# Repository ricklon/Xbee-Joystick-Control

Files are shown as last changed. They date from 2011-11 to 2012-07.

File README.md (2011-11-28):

#Xbee Joystick Controlled Robot

This project configures a set of Xbees that are plugged into a custom Joystick PCB, and wired on top of a line following Arduino based robot.
The robot project is here: http://ieee.rutgers.edu/content/line-following-kit

The current custom circuit boards for the project are kept in the Fritzing folder. In there there is a Fritzing for the Joystick, list of materials, and example etchable PCB files.

In order to wire the Xbee to the Arduino board you'll need to either use the custom circuit board in the Fritzing file, or you can bread board it on thop of the motor shield.

##Xbee programming for receiver, and sending

Note: This project currently uses Xbee series 1. They work fine and are well documented. 
I recommend using the Xbee Explorer (USB) or the Adafruit Xbee Adapter Kit (FTDI).

You will need a terminal program to configure the Xbees. One program that works on Windows, Mac, and Linux is Cool Term. You can find it here: http://freeware.the-meiers.org/

The configuration for the reciever Xbee should be:
+++//Wait for the OK, do not hit enter

```
+++ 
ATDL407B2C9A,DH0013A200,ID 2001,MY20, WR, CN
```

The configuraiton for the Joystick sender Xbee should be:
+++//Wait for the OK, do not hit enter

```
+++
ATDL407E10E6, DH0013A200, ID2001, MY10, D02, D12, D22, IR64, WR, CN
```

You can check the Xbee configuration with the following:
+++//Wait for the OK, do not hit enter

```
+++
ATDL, DH, ID, MY, D0, D1, D2, IR, CN
```

##Xbee robot receiver configuration
The bread boarding step requires the following parts:
Xbee breadboard adapter
4 wires
tiny breadboard

The Xbee adapter is wired in with the following pins:
Xbee --> Arduino
pin 1  -> 3.3v
pin 10 -> ground
pin 2 -> 0
pin 3 -> 1

It's easiest to do the wiring first. Then place the Xbee adapter on the tiny breadboard.

##Arduino Sketch
Make sure the Xbee Rx,Tx pins are disconneted from the Arduino. The Arduino Uno use the default serial port for Xbee and programming Arduino.

The upload the following sketch for the Joystick controls:
https://github.com/ricklon/Xbee-Joystick-Control/blob/master/arduino/XbeeControlledRobot256uno/XbeeControlledRobot256uno.pde

##Python code
This is only needed to diagnose communication issues. Not needed, but interesting.

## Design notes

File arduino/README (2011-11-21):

Each of these files are examples of elements need to debug the Xbee controlled robot.

The completed robot that will work on all Arduino's using the IEEE Rutgers  motorshield can use:
XbeeControledRobot256uno

The controls work OK.

The configuration for the reciever Xbee should be:
+++
ATDL407B2C9A,DH0013A200,ID 2001,MY20, WR, CN

The configuraiton for the Joystick sender Xbee should be:
+++
ATDL407E10E6, DH0013A200, ID2001, MY10, D02, D12, D22, IR64, WR, CN

You can check the Xbee configuration with the following:
+++
ATDL, DH, ID, MY, D0, D1, D2, IR, CN

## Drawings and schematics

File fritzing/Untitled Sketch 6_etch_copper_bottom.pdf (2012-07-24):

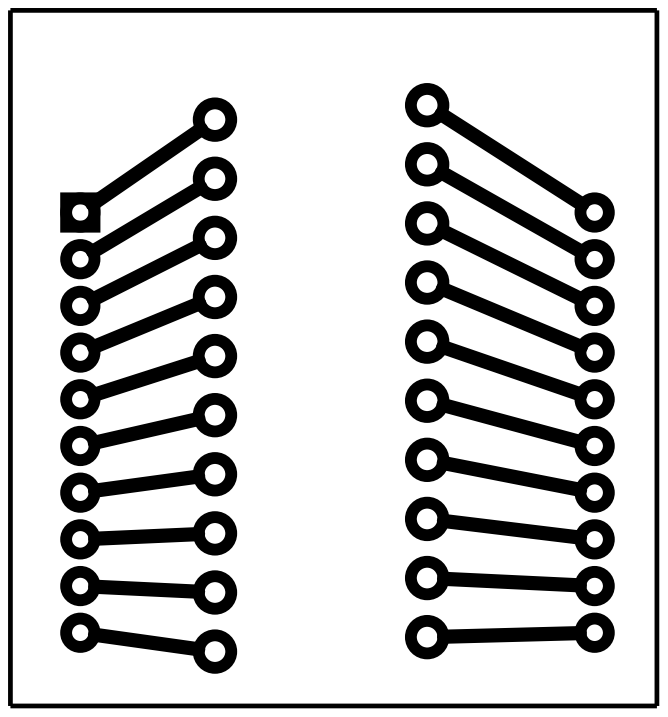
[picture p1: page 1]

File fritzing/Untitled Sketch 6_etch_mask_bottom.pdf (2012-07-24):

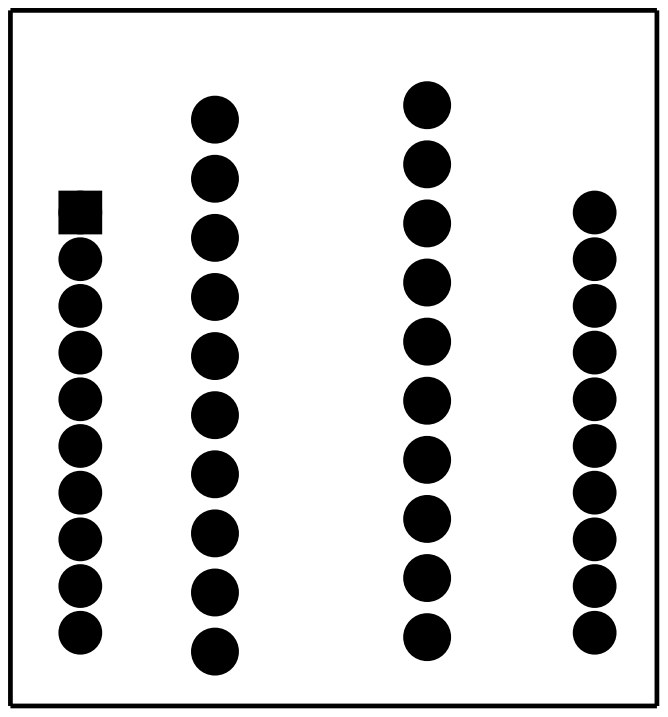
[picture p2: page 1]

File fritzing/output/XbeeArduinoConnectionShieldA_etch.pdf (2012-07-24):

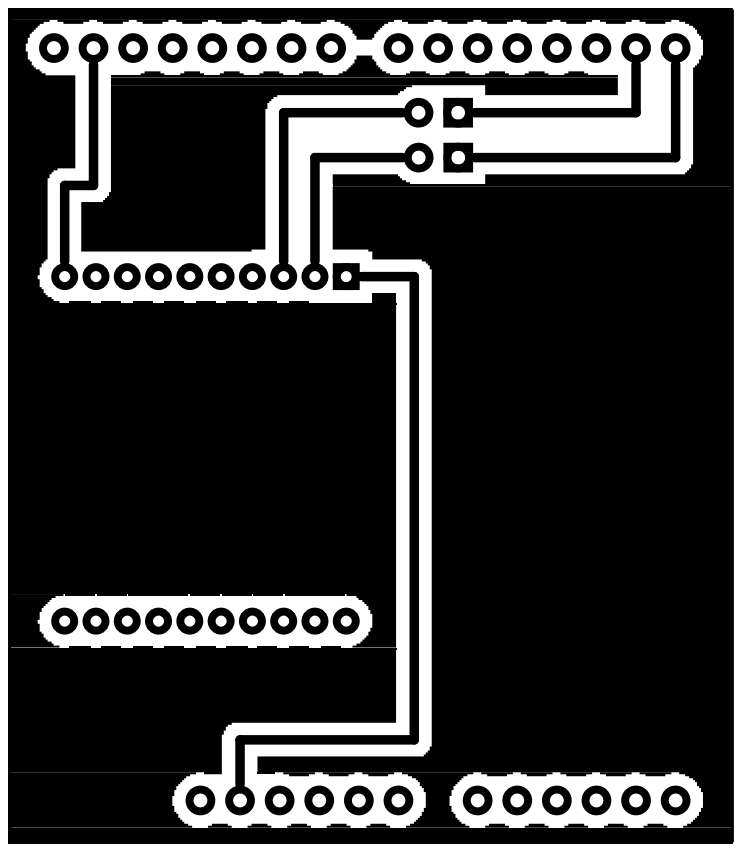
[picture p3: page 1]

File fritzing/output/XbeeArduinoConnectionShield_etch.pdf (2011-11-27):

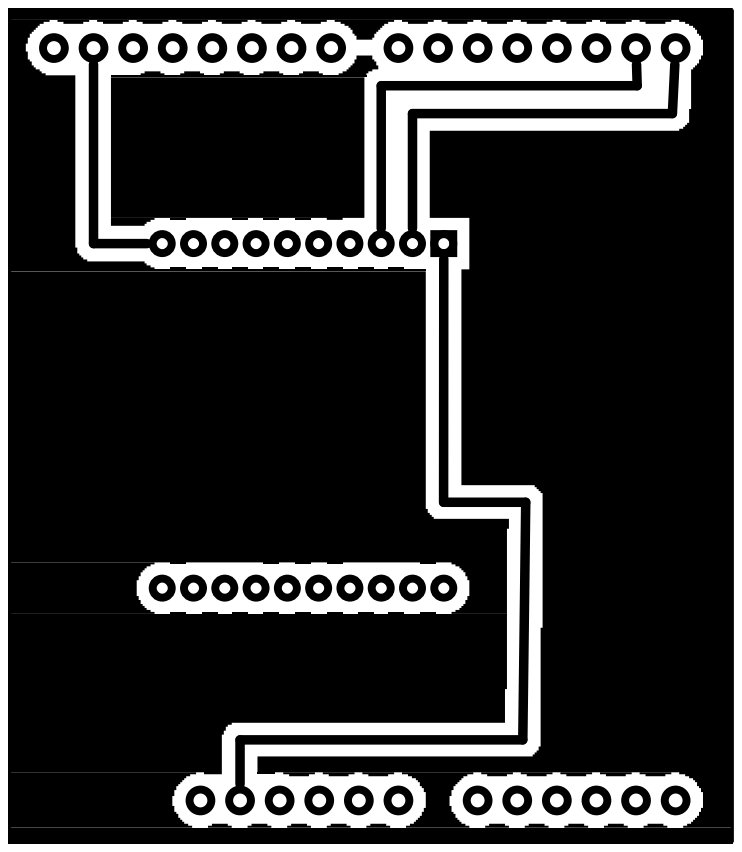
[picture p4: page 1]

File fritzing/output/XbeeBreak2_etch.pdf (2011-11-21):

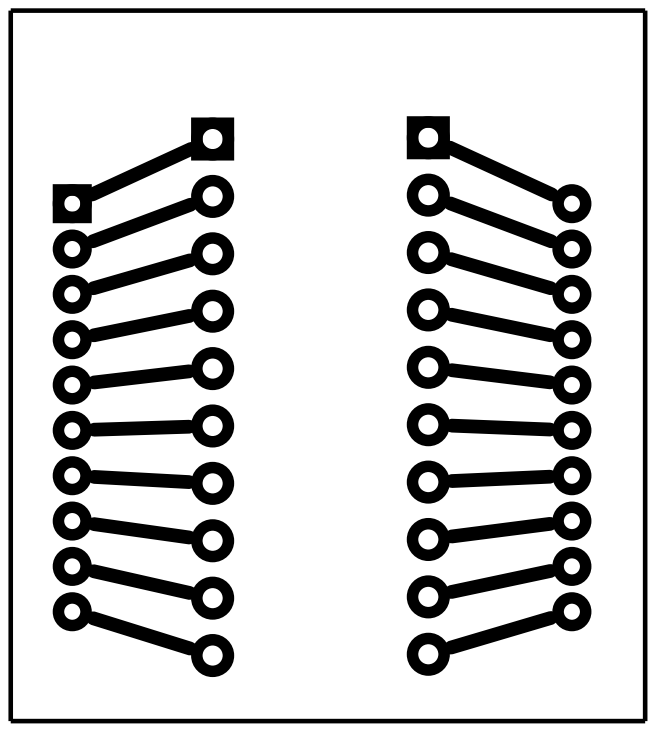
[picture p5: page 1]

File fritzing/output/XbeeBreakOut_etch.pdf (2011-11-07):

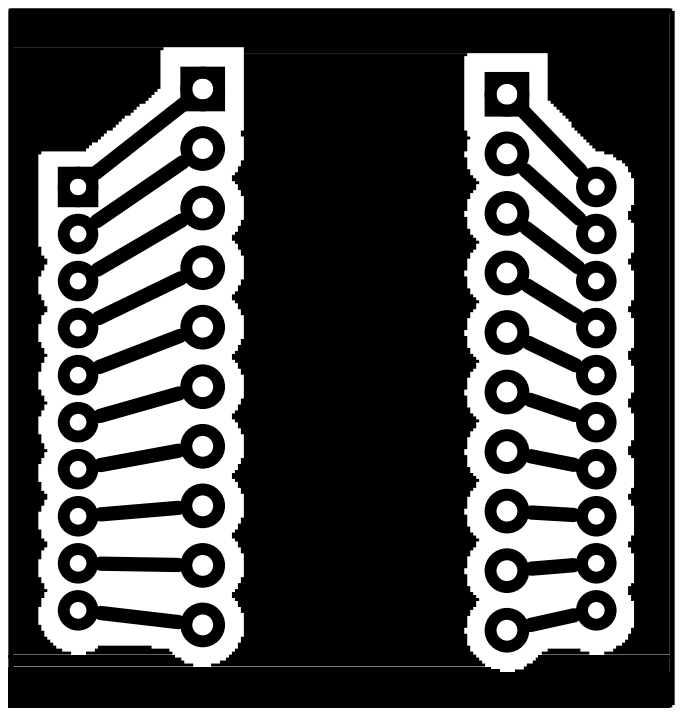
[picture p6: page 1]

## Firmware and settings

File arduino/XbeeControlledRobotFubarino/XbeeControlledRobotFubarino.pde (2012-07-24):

#define motor1Dir 2
#define motor1Enable 3
#define motor1PWM 4


#define motor2Dir 8
#define motor2Enable 5
#define motor2PWM 7


#define DEADZONE 25

const int packetLength = 22;	// XBee data messages will be 22 bytes long 
int dataPacket[packetLength]; //arraytoholdtheXBeedata 
int byteCounter = 0;	// counter for bytes received from the XBee

struct Position {
  int    xx;
  int    yy;
  boolean dirty;
};

int rl; //right left motion
int fb; //forwad back motion

void initMotorDriver()
{
  pinMode(motor1Dir, OUTPUT);
  pinMode(motor2Dir, OUTPUT);

  pinMode(motor1Enable, OUTPUT);
  pinMode(motor2Enable, OUTPUT);
  digitalWrite(motor1Enable,HIGH);
  digitalWrite(motor2Enable,HIGH);
  setLeftMotorSpeed(0); // make sure the motors are stopped
  setRightMotorSpeed(0);
}



void setMotorVel(int dirPin, int pwmPin, int velocity)
{
  if (velocity >= 255) velocity = 255;
  if (velocity <= -255) velocity = -255;

  if (velocity == 0)
  {
    digitalWrite(dirPin, HIGH);
    digitalWrite(pwmPin, HIGH);
  }
  else if(velocity <0){ // Reverse
    digitalWrite(dirPin, HIGH);
    analogWrite(pwmPin, 255+velocity);
  }
  else if(velocity >0){ // Forward
    digitalWrite(dirPin,LOW);
    analogWrite(pwmPin, velocity);
  }

}


void setLeftMotorSpeed(int velocity)
{
  //Serial.print("Set Left: ");
  //Serial.println(velocity);
  setMotorVel(motor1Dir, motor1PWM, -velocity);

}

void setRightMotorSpeed(int velocity)
{
  //Serial.print("Set Right: ");
  //Serial.println(velocity);
  setMotorVel(motor2Dir, motor2PWM, -velocity);
}

void getJoystickData( struct Position& xxyy) 
{ 
  int inByte;
  // read incoming byte: 
  int byte_cnt = 0;

  xxyy.dirty = true;
  while (Serial.available() > 0)
  {

    inByte = Serial.read();


    // beginning of a new packet is 0x7E: 
    if (inByte == 0x7E ) 
    {
      dataPacket[0]= inByte; 
      for (byte_cnt = 1; byte_cnt < 22; byte_cnt++)
      {
        while (Serial.available() == 0)
        {
        } 
        dataPacket[byte_cnt] = Serial.read();
      }
      //-Serial.print("VertY Dec: ");
      xxyy.xx = dataPacket[11] *256 + dataPacket[12]; 
      //-Serial.print(xxyy.xx); 
      //-Serial.print(" ");
      //-Serial.print("HorX Dec: ");
      xxyy.yy = dataPacket[13] *256 + dataPacket[14]; 
      //-Serial.print(xxyy.yy); 
      //-Serial.println();
      xxyy.dirty = false;
    }
  }
}


void setup()
{
  // start serial communications: 
  Serial.begin(9600);
  Serial.println("Robot Setup");
  //Serial1.begin(9600);

  // prints title with ending line break
  /*
  Serial.println("Line Sensor boar Sensor test");
   Serial.println("Enter to show sensor value: 0=Sensor0, 1=Sensor1, 2=Sensor2, 3=Sensor3, 4=Sensor4, 5=Sensor5");
   Serial.println("Enter to move: s= stop, f = forward, r = right, l = left");
   */
  initMotorDriver();
  
    
  setRightMotorSpeed(255); 
  setLeftMotorSpeed(-255);
  delay(500);
  setRightMotorSpeed(-255); 
  setLeftMotorSpeed(255);
  delay(500);
  setRightMotorSpeed(0); 
  setLeftMotorSpeed(0); 
}

void loop() 
{ 
  struct Position xxyy = 
  {
    0 , 0 , true   
  };

  getJoystickData(xxyy);
  if (xxyy.dirty == false)
  {

    //calibrate the range so the resting position is 0 movement
    fb = map(xxyy.xx + 43, 0, 1023, -255, 255) ;
    rl = map(xxyy.yy + 43, 0, 1023, -255, 255) ;
    
    //horizontal band
    //Check if in fb deadzone
    if (rl < DEADZONE && rl > -DEADZONE) 
    {
      //Check if in rl deadzone
      if (fb < DEADZONE && fb > -DEADZONE)
      {
        setRightMotorSpeed(0); 
        setLeftMotorSpeed(0);
      }
      else //Go forward or back
      {
        Serial.println("Full Forward or Back");
        setRightMotorSpeed(fb); 
        setLeftMotorSpeed(fb);
        delay(100);
      }
    }
    else
    {
      Serial.println("Right RL zone"); 
      if(rl>DEADZONE)
      {
        if (fb > DEADZONE)
        {
          Serial.println("Upper Right RL zone"); 
          setRightMotorSpeed(0); 
          setLeftMotorSpeed(fb); 
        }
        if  (fb < -DEADZONE)
        {
          Serial.println("Lower Right RL zone"); 
          setRightMotorSpeed(0); 
          setLeftMotorSpeed(fb); 
        }
      }
      else
      {
        Serial.println("Left RL Zone"); 
        if (fb > DEADZONE)
        {
          Serial.println("Upper Left RL zone"); 
          setRightMotorSpeed(fb); 
          setLeftMotorSpeed(0); 
        }
        if  (fb < -DEADZONE)
        {
          Serial.println("Lower Left RL zone"); 
          setRightMotorSpeed(fb); 
          setLeftMotorSpeed(0); 
        }
      }        
      if (fb < DEADZONE && fb > -DEADZONE)
      {
        setRightMotorSpeed(rl); 
        setLeftMotorSpeed(-rl); 
       }
    
    }
   
 

    Serial.print("fbX: ");
    Serial.print(fb);
    Serial.print(" : ");
    Serial.print(xxyy.xx);
    Serial.print(" rlY: ");
    Serial.print(rl);
    Serial.print(" : ");
    Serial.println(xxyy.yy);
 /*   
    Serial.print ("setRightMotorSpeed: ");
    Serial.print (map(xx, -2,4, -255,255)); 
     Serial.print(" setLeftMotorSpeed: ");
     Serial.println(map(yy,-2, 4, -255, 255)); 
    */

    delay(10);
  }
}

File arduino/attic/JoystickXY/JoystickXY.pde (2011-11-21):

int xPin = 9;    // LED connected to digital pin 9
int yPin = 11;   // LED connected to digital pin 11

int photoPin = 0;
int xPot = 1;
int yPot = 2;

int photoVal = -1;
int xx, yy = -1;
int minmax, ymax, xmax = 0;

void setup() {
  Serial.begin(9600);
  Serial.println("Start");
  
  pinMode(xPin, OUTPUT);     
  pinMode(yPin, OUTPUT);     
  digitalWrite(xPin, HIGH);
  digitalWrite(yPin, HIGH);

  digitalWrite(xPin, LOW);
  delay(500);
  xmax = analogRead(photoPin);
  digitalWrite(xPin, HIGH);

  digitalWrite(yPin, LOW);
  delay(500);
  ymax = analogRead(photoPin);
  digitalWrite(yPin, HIGH);
  
   sendMax();
   minmax = min(xmax, ymax);
   setXY(255, 255);
}

void setXY(int xx, int yy) 
{
  xx = map(xx, 0, minmax, 255, 0);
  yy = map(yy, 0, minmax,  255, 0);
  
  //For some reason some values were mapping negative
  constrain(xx, 0, 255);
  constrain(yy, 0, 255);
  
  analogWrite(xPin, xx);
  analogWrite(yPin, yy);
  sendXY(xx, yy);
}

void sendXY(int xx, int yy) 
{
      Serial.print(" { \"xx\" : ");
      Serial.print(xx);
      Serial.print(", \"yy\" : ");
      Serial.print(yy);
      Serial.println("}");
}

void sendMax()
{

    Serial.print(" { \"xmax\" : ");
    Serial.print(xmax);
    Serial.print(", \"ymax\" : ");
    Serial.print(ymax);
    Serial.println("}");
}



void loop() 
{
  xx = analogRead(xPot);
  yy = analogRead(yPot);
  setXY(xx, yy);
  
}

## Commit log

2011-11-07 Xbee joystick fritzing design added.
    [XBEEJoystick-half.fz]
2011-11-07 Xbee Breakout Board added.
    [XbeeBreakOut.fz]
2011-11-13 Xbee series 1 needs to have VREF attached to the 3.3v line.
    [XBEEJoystick-half.fz]
2011-11-21 Way to many things added. Working robot sketch XbeeControledRobot256uno
    [XbeeBreak2.fz, XbeeBreakOutStatusLED.fz]
2011-11-21 Xbee joystick PCB, and breadboard updates to accomodate the pullup button from JOystick to Xbee.
    [XBEEJoystick-half.fz, XbeeBreakOutStatusLED.fz]
2011-11-21 Added the custom Xbee Arduino Shield to connect XBee to the Arduino robot.
    [XbeeArduinoConnectionShield.fz]
2011-11-27 Cleaned up the Fritzing folder.
    [XbeeBreak2.fz, XbeeBreakOut.fz]
2011-11-28 Fixed typo about controled vs controlled.
    [XbeeControlledRobot256uno.pde]
2012-07-24 Added a startup line.
    Updated frizzing sketch.
    [XBEEJoystick-half.fzz, XbeeArduinoConnectionShield.fzz, XbeeArduinoConnectionShieldA.fz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]
